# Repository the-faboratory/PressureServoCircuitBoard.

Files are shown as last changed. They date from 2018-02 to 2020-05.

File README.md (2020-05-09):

# Pneumatic Regulator git repository
This repository contains (hopefully) everything needed to replicate the pneumatic regulator presented in

J. W. Booth, J. C. Case, E. L. White, D. S. Shah, and R. Kramer-Bottiglio, “[An addressable pneumatic regulator for distributed control of soft robots](10.1109/ROBOSOFT.2018.8404892),” in 2018 IEEE International Conference on Soft Robotics (RoboSoft).

It will be called "pneumatic regulator" and "pressure regulator" interchangeably.

If you have comments, suggestions, or want additional information, including how to obtain a pre-programmed and pre-assembled pressure regulator, please contact Joran Booth at JoranBooth@gmail.com. Being a research lab affiliated with a non-profit university, we are unable to sell regulators through our Yale affiliations. However, we are exploring commercializing the boards out of a small garage operation, depending on interest levels and applicable laws.

## Getting Started

### Prerequisites

Download MPLAB IDE(http://www.microchip.com/mplab/mplab-x-ide), with the XC compilers.

A detailed programming guide, with notes on the PressureRegulator's state machine, is in repository_guide.docx.

There are two versions of the hardware, with different connectors: one with 0.1" headers, and one with a MOLEX connector.

### Installing / Using
Programming a device is as easy as 1,2,3,...4:
```
1. Open the PIC_I2C.X project in MPLAB.
2. Change the variable I2C_ADDRESS to contain 2x the address you want the Arduino to call your PIC. Example: Arduino talks to sensor at address 8. I2C_ADDRESS = 2x8 = 16
3. Click "clean and build" to make sure it is compiling properly for your computer. (If you get a compiler error, try opening project properties and use C standard 90 (Project properties -> XC8 Global Options -> C Standard))
4. Click "Make and Program Device Main Project", to download the program to your PIC using a PicIt3 (the 'red box').
```

## Testing The Firmware

For your first test, use the Arduino driver pneumatic_regulator_driver.ino, or the sample Arduino Wire library code. For your I2C pullup, use 3.3k or 4.7k.

## Explanation of files (see each file for details):

File/Directory |  Purpose |
----- | --------- |
arduino_driver | Folder containing sample Arduino driver for communicating with the pressure regulators
auxiliary_files | Additional documentation, and a Microchip I2C application note.
pcb_files | Eagle files, bill of materials, and gerber files (for PCB.ng) for both versions of the regulator: 0.1" headers, and MOLEX connector
Pic_I2C.X | Project folder for programming the pneumatic regulator's PIC microcontroller using MPLAB.
PicIt3_user_guide | [A guide to using the PICkit3](http://ww1.microchip.com/downloads/en/DeviceDoc/50002010B.pdf). Made by Microchip.
pressure_regulator_i2c.c | Firmware for the pressure regulator's PIC microcontroller, to control pressure manually or use Bang-Bang with a deadband to regulate the pressure at the output (i.e., in your actuator).
repository_guide.docx | An explanation of how to download firmware to a PIC, using this repository.

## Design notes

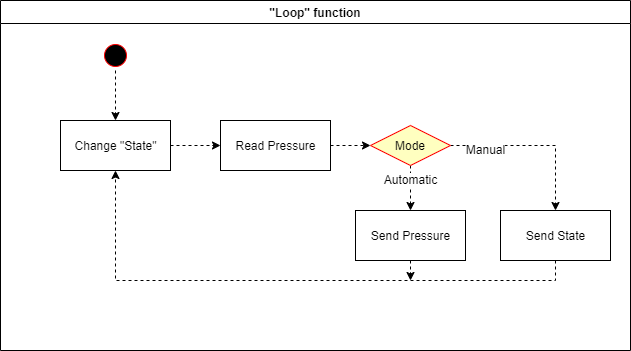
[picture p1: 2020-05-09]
auxiliary_files/pneumatic_regulator_state_flowchart.png

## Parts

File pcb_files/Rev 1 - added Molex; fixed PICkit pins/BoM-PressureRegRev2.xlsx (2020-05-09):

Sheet: 30PSI
Description | DigiKey Description | DigiKey part # | Manufacturer | Mfg part # | Qty | $/unit | Total | Packaging | Link
10K Ohm resistor | RES SMD 10K OHM 1% 1/10W 0603 | 311-10.0KHRCT-ND | Yageo | RC0603FR-0710KL | 2 | 0.015 | 0.03 | Cut reel | https://www.digikey.com/products/en?keywords=%20311-10.0KHRCT-ND%20
10uf Capacitor | CAP TANT 10UF 25V 20% 1206 | 478-8496-1-ND | AVX | F951E106MAAAQ2 | 1 | 0.766 | 0.766 | Cut reel | https://www.digikey.com/products/en?keywords=478-8496-1-ND
10uh Inductor | FIXED IND 10UH 230MA 1.3 OHM SMD | 490-6588-1-nd | Murata | LQH31CN100K03L | 2 | 0.685 | 1.37 | Cut reel | https://www.digikey.com/products/en?keywords=490-6588-1-nd
150 Ohm resistor | RES SMD 150 OHM 1% 1/10W 0603 | 311-150HRCT-ND | Yageo | RC0603FR-07150RL | 1 | 0.015 | 0.015 | Cut reel | https://www.digikey.com/products/en?keywords=490-6588-1-nd
1uf Capacitor | CAP CER 1UF 25V X5R 0603 | 311-1445-1-ND | Yageo | CC0603KRX5R8BB105 | 3 | 0.052 | 0.156 | Cut reel | https://www.digikey.com/products/en?keywords=311-1445-1-ND%20
Diode | DIODE GEN PURP 75V 200MA SOD523 | bas16xv2t5gosct-nd | ON Semiconductor | BAS16XV2T5G | 2 | 0.156 | 0.312 | Cut reel | https://www.digikey.com/products/en?keywords=bas16xv2t5gosct-nd
Cap 100uf | CAP ALUM 100UF 20% 35V SMD | pce5016ct-nd | Panasonic | EEE-FT1V101AP | 2 | 0.427 | 0.854 | Cut reel | https://www.digikey.com/products/en?keywords=pce5016ct-nd
Connection header | CONN HEADER 4POS 1.25MM R/A SMD | WM7622CT-ND | Molex | 532610471 | 1 | 1.038 | 1.038 | Cut reel | https://www.digikey.com/products/en?keywords=WM7622CT-ND
PIC microchip | IC MCU 8BIT 14KB FLASH 14-TSSOP | PIC16F1825T-I/STCT-ND | Microchip | PIC16F1825T-I/ST | 1 | 1.45 | 1.45 | Cut reel | https://www.digikey.com/products/en?keywords=PIC16F1825T-I%2FSTCT-ND
IC Voltage regulator 5V | IC REG LINEAR 5V 100MA SOT223 | 576-1249-1-nd | Microchip | MIC5200-5.0YS-TR | 1 | 1.08 | 1.08 | Cut reel | https://www.digikey.com/products/en?keywords=576-1249-1-nd
Green LED | LED GREEN CLEAR 0603 SMD | 160-1435-1-nd | Lite-On | LTST-C190KGKT | 1 | 0.196 | 0.196 | Cut reel | https://www.digikey.com/products/en?keywords=160-1435-1-nd
n-ch Mosfet 100v 17a | MOSFET N-CH 100V 17A DPAK | irlr3410pbfct-nd | International Rectifier | IRLR3410TRPBF | 2 | 0.88 | 1.76 | Cut reel | https://www.digikey.com/products/en?keywords=irlr3410pbfct-nd
Parker X-valve | N/A - select 30psi, 3 way universal, long pins, 12 VDC | N/A | Parker | 912-000001-003 | 2 | 37 | 74 | Tray | http://ph.parker.com/us/12051/en/x-valve-miniature-pneumatic-solenoid-valve
Pressure sensor, 5V, 30psi | SENSOR PRESS 30PSIG ANALOG | 480-4490-ND | Honeywell | ASDXRRX030PGAA5 | 1 | 46.95 | 46.95 | Tray | https://www.digikey.com/product-detail/en/honeywell-sensing-and-productivity-solutions/ASDXRRX030PGAA5/480-4490-ND/2566947
 |  |  |  |  |  |  | 129.977

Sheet: 100PSI
These parts have not been tested together! Power requirements and orifice sizes should be identical.
Description | DigiKey Description | DigiKey part # | Manufacturer | Mfg part # | Qty | $/unit | Total | Packaging | Link
10K Ohm resistor | RES SMD 10K OHM 1% 1/10W 0603 | 311-10.0KHRCT-ND | Yageo | RC0603FR-0710KL | 2 | 0.015 | 0.03 | Cut reel | https://www.digikey.com/products/en?keywords=%20311-10.0KHRCT-ND%20
10uf Capacitor | CAP TANT 10UF 25V 20% 1206 | 478-8496-1-ND | AVX | F951E106MAAAQ2 | 1 | 0.766 | 0.766 | Cut reel | https://www.digikey.com/products/en?keywords=478-8496-1-ND
10uh Inductor | FIXED IND 10UH 230MA 1.3 OHM SMD | 490-6588-1-nd | Murata | LQH31CN100K03L | 2 | 0.685 | 1.37 | Cut reel | https://www.digikey.com/products/en?keywords=490-6588-1-nd
150 Ohm resistor | RES SMD 150 OHM 1% 1/10W 0603 | 311-150HRCT-ND | Yageo | RC0603FR-07150RL | 1 | 0.015 | 0.015 | Cut reel | https://www.digikey.com/products/en?keywords=490-6588-1-nd
1uf Capacitor | CAP CER 1UF 25V X5R 0603 | 311-1445-1-ND | Yageo | CC0603KRX5R8BB105 | 3 | 0.052 | 0.156 | Cut reel | https://www.digikey.com/products/en?keywords=311-1445-1-ND%20
Diode | DIODE GEN PURP 75V 200MA SOD523 | bas16xv2t5gosct-nd | ON Semiconductor | BAS16XV2T5G | 2 | 0.156 | 0.312 | Cut reel | https://www.digikey.com/products/en?keywords=bas16xv2t5gosct-nd
Cap 100uf | CAP ALUM 100UF 20% 35V SMD | pce5016ct-nd | Panasonic | EEE-FT1V101AP | 2 | 0.427 | 0.854 | Cut reel | https://www.digikey.com/products/en?keywords=pce5016ct-nd
Connection header | CONN HEADER 4POS 1.25MM R/A SMD | WM7622CT-ND | Molex | 532610471 | 1 | 1.038 | 1.038 | Cut reel | https://www.digikey.com/products/en?keywords=WM7622CT-ND
PIC microchip | IC MCU 8BIT 14KB FLASH 14-TSSOP | PIC16F1825T-I/STCT-ND | Microchip | PIC16F1825T-I/ST | 1 | 1.45 | 1.45 | Cut reel | https://www.digikey.com/products/en?keywords=PIC16F1825T-I%2FSTCT-ND
IC Voltage regulator 5V | IC REG LINEAR 5V 100MA SOT223 | 576-1249-1-nd | Microchip | MIC5200-5.0YS-TR | 1 | 1.08 | 1.08 | Cut reel | https://www.digikey.com/products/en?keywords=576-1249-1-nd
Green LED | LED GREEN CLEAR 0603 SMD | 160-1435-1-nd | Lite-On | LTST-C190KGKT | 1 | 0.196 | 0.196 | Cut reel | https://www.digikey.com/products/en?keywords=160-1435-1-nd
n-ch Mosfet 100v 17a | MOSFET N-CH 100V 17A DPAK | irlr3410pbfct-nd | International Rectifier | IRLR3410TRPBF | 2 | 0.88 | 1.76 | Cut reel | https://www.digikey.com/products/en?keywords=irlr3410pbfct-nd
Parker X-valve | N/A - select 100psi, 3 way universal, long pins, 12 VDC | N/A | Parker | 912-000001-021 | 2 | 37 | 74 | Tray | http://ph.parker.com/us/12051/en/x-valve-miniature-pneumatic-solenoid-valve
Pressure sensor, 5V, 100psi | SENSOR PRESS 100PSIG ANALOG | 480-3748-ND | Honeywell | ASDXRRX100PGAA5 | 1 | 49.27 | 49.27 | Tray | https://www.digikey.com/product-detail/en/honeywell-sensing-and-productivity-solutions/ASDXRRX100PGAA5/480-3748-ND/2566950
 |  |  |  |  |  |  | 132.297

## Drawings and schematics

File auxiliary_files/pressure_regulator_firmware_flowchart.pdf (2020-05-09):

11/15/2017 | pressureRegulatorI2cFlowchart.xml

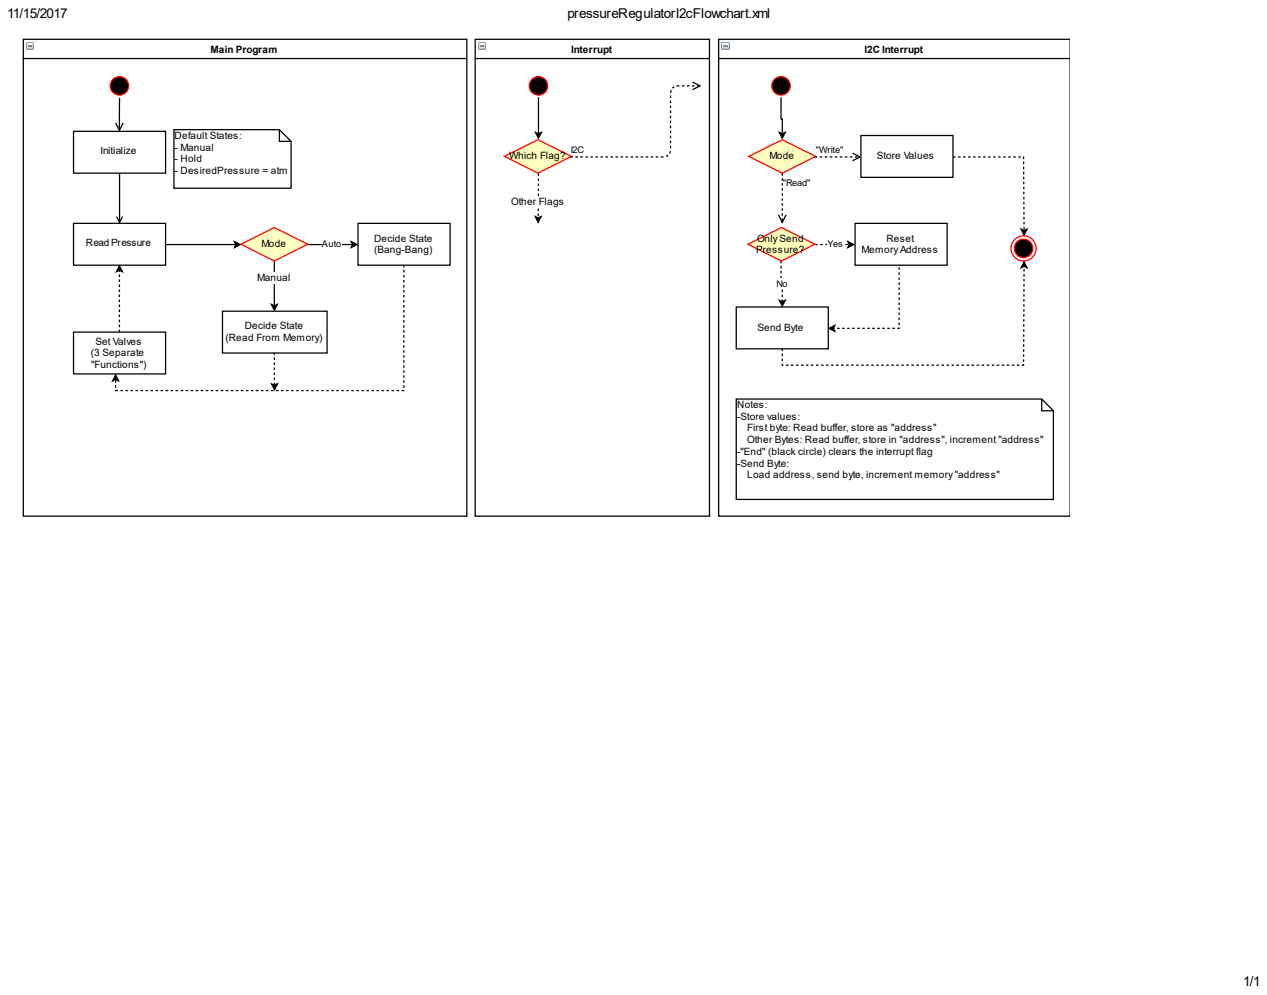
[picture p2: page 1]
Main Program; Initialize; Read Pressure; Default States: - Manual - Hold - DesiredPressure = atm; Auto; Manual; Mode; Decide State (Bang-Bang); Set Valves (3 Separate "Functions"); Interrupt; Which Flag?; I2C Interrupt; "Write"; "Read"; Store Values; Yes; Only Send Pressure?; Send Byte; Other Flags

Reset Memory Address

Decide State
(Read From Memory)

Notes:
-Store values:
First byte: Read buffer, store as "address" Other Bytes: Read buffer, store in "address", increment "address"

-"End" (black circle) clears the interrupt flag
-Send Byte:
Load address, send byte, increment memory "address"

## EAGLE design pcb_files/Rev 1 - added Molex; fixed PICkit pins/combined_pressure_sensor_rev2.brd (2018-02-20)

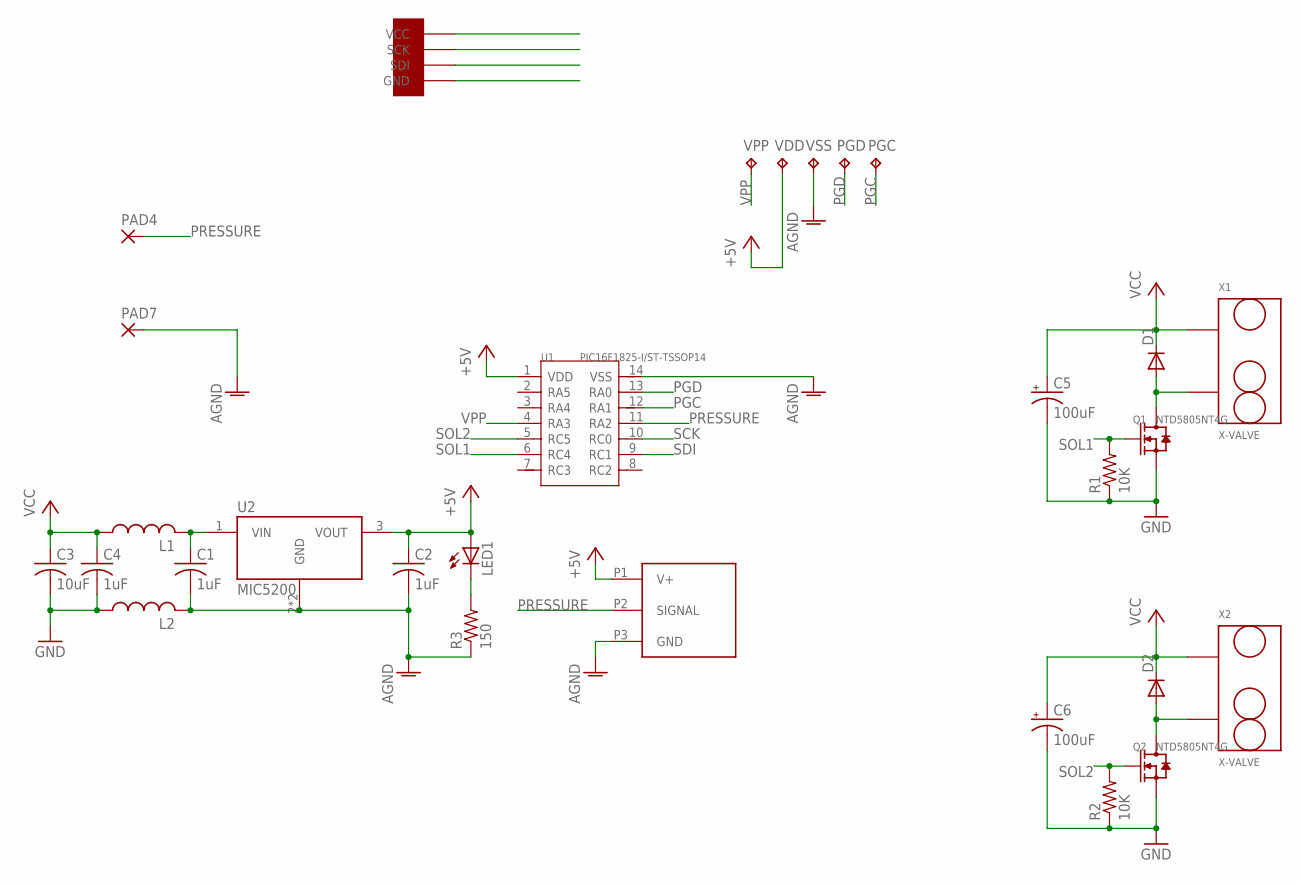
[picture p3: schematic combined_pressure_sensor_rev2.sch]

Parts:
C1, C2, C4: 1uF; C0603
C3: 10uF; C1206
C5, C6: 100uF; 153CLV-0605
D1, D2: DIODE-SOD523; SOD523
L1, L2: L-USL1206; L1206
LED1: LEDCHIP-LED0603; CHIP-LED0603
PAD4, PAD7: SMD2; SMD1,27-2,54
PGC: TPB1,27; B1,27
PGD: TPB1,27; B1,27
Q1, Q2: NTD5805NT4G; DPAK
R1, R2: 10K; R0603
R3: 150; R0603
U1: PIC16F1825-I/ST-TSSOP14; TSSOP14-0.65-5X4.4MM
U2: MIC5200; SOT223
U$1: PICOBLADE4POS1.25MMRIGHTANGLESURFACE; PICOBLADE4POSMALEHEADER
U$3: ASDX
VDD: TPB1,27; B1,27
VPP: TPB1,27; B1,27
VSS: TPB1,27; B1,27
X1, X2: X-VALVE

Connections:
+5V: C2.1, LED1.A, U1.1 (VDD), U2.3 (VOUT), U$3.P1 (V+), VDD.TP
AGND: C1.2, C2.2, L2.2, PAD7.1, R3.1, U1.14 (VSS), U2.2 (GND), U2.4 (GND), U$3.P3 (GND), VSS.TP
GND: C3.2, C4.2, C5.-, C6.-, L2.1, Q1.2 (S), Q2.2 (S), R1.1, R2.1, U$1.GND
unnamed: D1.A, Q1.3 (D), X1.P$2
unnamed: D2.A, Q2.3 (D), X2.P$2
unnamed: C1.1, L1.2, U2.1 (VIN)
unnamed: LED1.C, R3.2
PGC: PGC.TP, U1.12 (RA1)
PGD: PGD.TP, U1.13 (RA0)
PRESSURE: PAD4.1, U1.11 (RA2), U$3.P2 (SIGNAL)
SCK: U1.10 (RC0), U$1.SCK
SDI: U1.9 (RC1), U$1.SDI
SOL1: Q1.1 (G), R1.2, U1.6 (RC4)
SOL2: Q2.1 (G), R2.2, U1.5 (RC5)
VCC: C3.1, C4.1, C5.+, C6.+, D1.C, D2.C, L1.1, U$1.VCC, X1.P$1, X2.P$1
VPP: U1.4 (RA3), VPP.TP

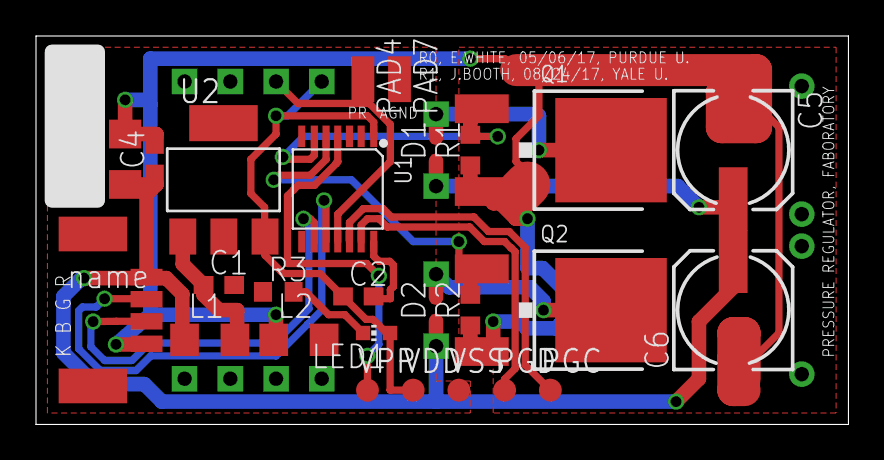
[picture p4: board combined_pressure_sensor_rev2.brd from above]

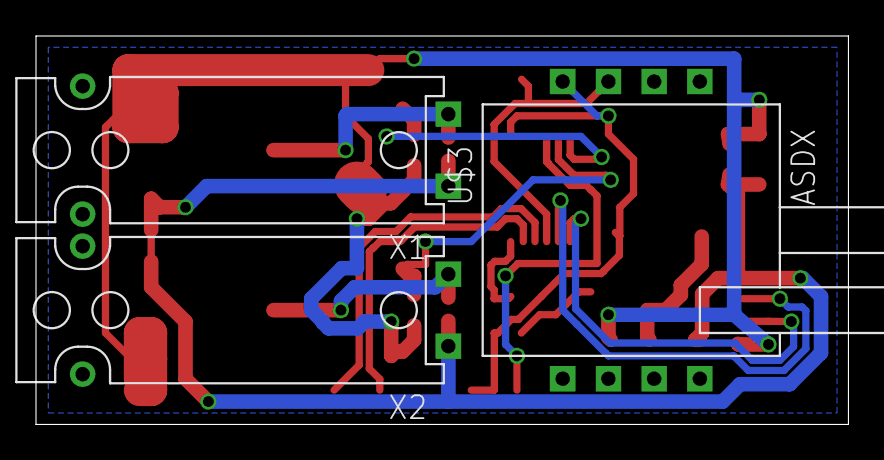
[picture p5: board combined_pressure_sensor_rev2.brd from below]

Board: 2 copper layers, 45.1 x 21.6 mm, 29 parts (3 on the bottom side), 16 nets.

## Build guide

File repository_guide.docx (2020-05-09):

Last edited 2020-05-09 by Dylan Shah.

# 1. Programming a PIC (and how to use I2C)

General Notes:

- Steps 1-8 describe MPLab and circuit setup. Step 9 describes communication methods.
- This tutorial is written for the capacitor board, but is mostly applicable to all Faboratory circuit boards with a PIC microcontroller
1. Power circuit board with an external power supply of 5.00 volts, at least 10 mA. The Arduino 5V output line is insufficient. (Limit the circuit to 100 mA or less, to avoid frying the board in case of short-circuit. If four sensors are plugged in and one is being programmed by the PICkit3, <0.013 A will be used.) Plug PICkit 3 into PC.

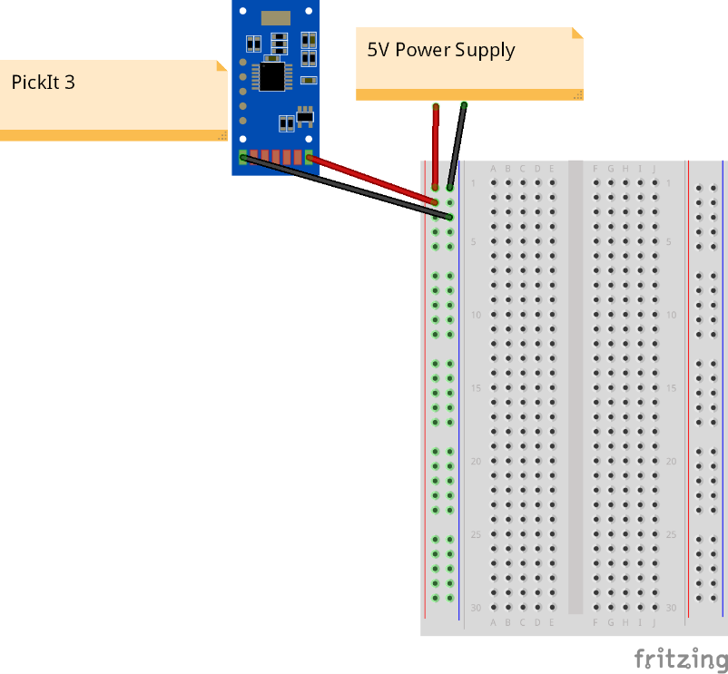
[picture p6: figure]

Figure 1. A suggested circuit. The blue PCB is the capacitor board or a pressure regulator. The white board is a breadboard.

2. Open Pic project <pic_i2c_project > in MPLab X IDE
3. Double-click the relevant “C” (.c) file to open it. In line 77, edit i2c_address to your desired address. In the photo below, the Arduino will communicate with address 99. It is stored in the PIC as address 198, since the Arduino automatically “shifts left” the address bits, i.e. it multiplies by 1 binary bit = value of 2.

Figure 2. Edit the I2C_ADDRESS variable.

4. Make sure there aren’t any hard-coded filepaths in the files, by right-clicking the project and doing “Clean and Build”

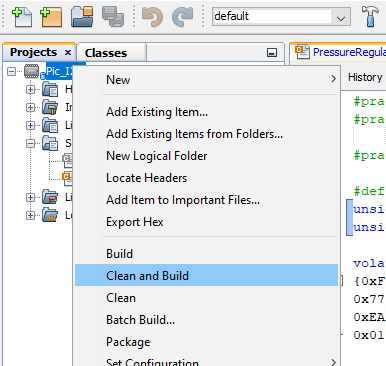
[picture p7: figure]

Figure 3. Prepare the project with “Clean and Build”

5. Set the PCB on a stable surface and firmly place the metal leads of the red PICkit 3 on the 5 circular pads of your PCB (Figure 4). Make sure all 5 leads contact their appropriate pad (but don’t break them).

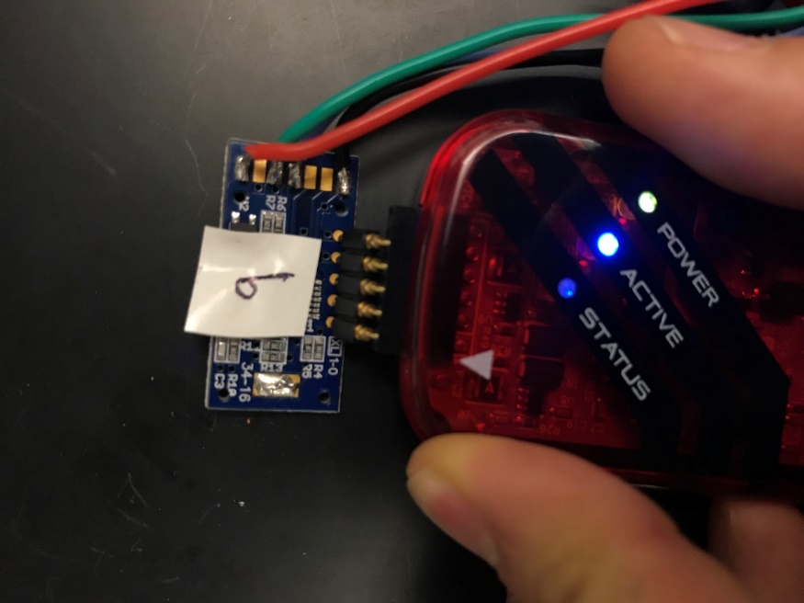
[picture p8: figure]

Figure 4. Connecting the PICit3 to the PCB.

6. Keeping the pads pressed, download to device using "Make and Debug Program Device".

Figure 5. Make and Debug Program Device

  a. If you didn’t already plug in the PICit3, a window will pop up. Plug in your PICit3, select it in the menu, and click “OK”.

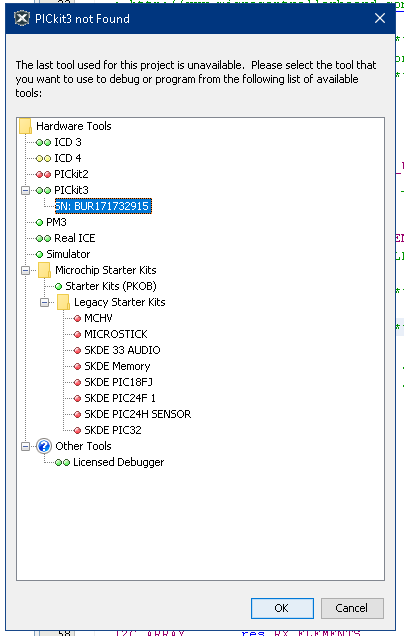
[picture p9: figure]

Figure 6. Selecting your PICkit3

  b. The console (probably at the bottom of your screen) will give you a message like “BUILD FAILED” or “BUILD SUCCESSFUL”. If the build failed , right-click your Project, select “clean and build”, and repeat this step.
    i. Other troubleshooting steps: 1. make sure you excluded all unnecessary files. 2. Make sure your board is powered by an external power supply, not the Arduino. 3. “Advanced” users: debug the firmware code.

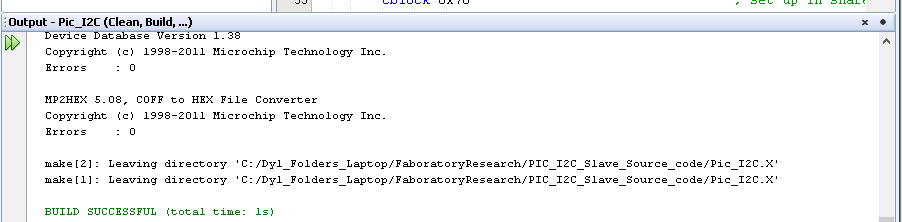
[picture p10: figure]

Figure 7. A “build successful” message.

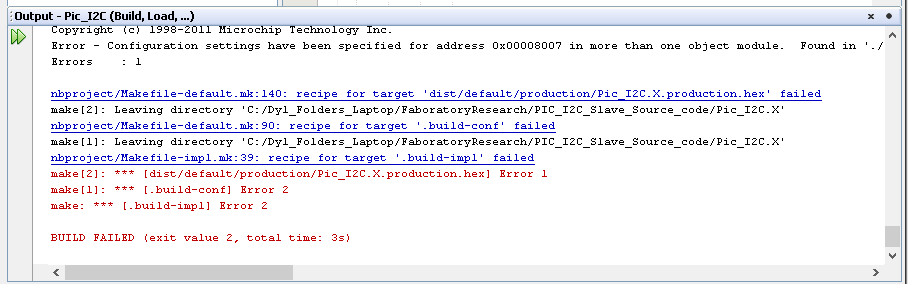
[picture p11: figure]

Figure 8. A "build failed” message.

7. Once it shows “build successful”, the console will clear and begin showing things like “Connecting to MPLAB PICkit 3”.

Figure 9. Connecting to PICkit 3

8. Some errors might show up.
  a. Basically , return to Step 4. Read the rest of bullet-point 8’s sub-bullets for additional tips.
  b. Shows red “Target device was not found…” Return to Step 4 (i.e, connect PIC and PICkit3, Make and Download…). Make sure to have good contact between each PICkit3 metal lead and the PCB’s corresponding circular contact.

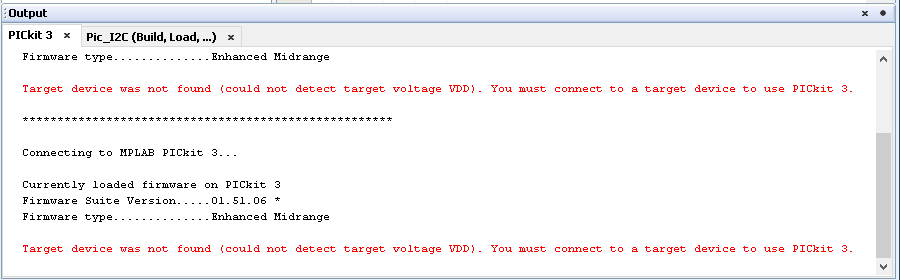
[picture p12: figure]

Figure 10. Target device not found.

  c. Popup similar to “Target Device ID (0x0) is an Invalid Device ID…”. DO NOT continue programming. Click Cancel, and return to step 4. Continuing can sometimes make the PIC un-programmable, but “when and why” is not well docmumented.

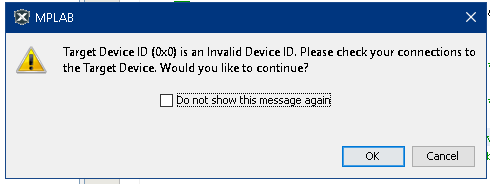
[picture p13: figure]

Figure 11. Target Device ID Invalid

9. Programming is complete when console displays “verify/program complete”.

Figure 12. Program/Verify complete

10. Optional: lift leads off of pads; power-cycle circuit. (I.e. turn the power supply off then on.) Sometimes the PIC will be put in a harmless but nonresponsive state during programming.
11. Connect the appropriate pins to an I2C circuit (“bus”). Arduino: A4 (SDA)=blue, A5(SCL) = green. Optionally, adjust so the PIC is powered by the Arduino. An example circuit is shown below. Typically I use 3.3KOhm pull-up resistors (https://electronics.stackexchange.com/questions/1849/is-there-a-correct-resistance-value-for-i2c-pull-up-resistors).

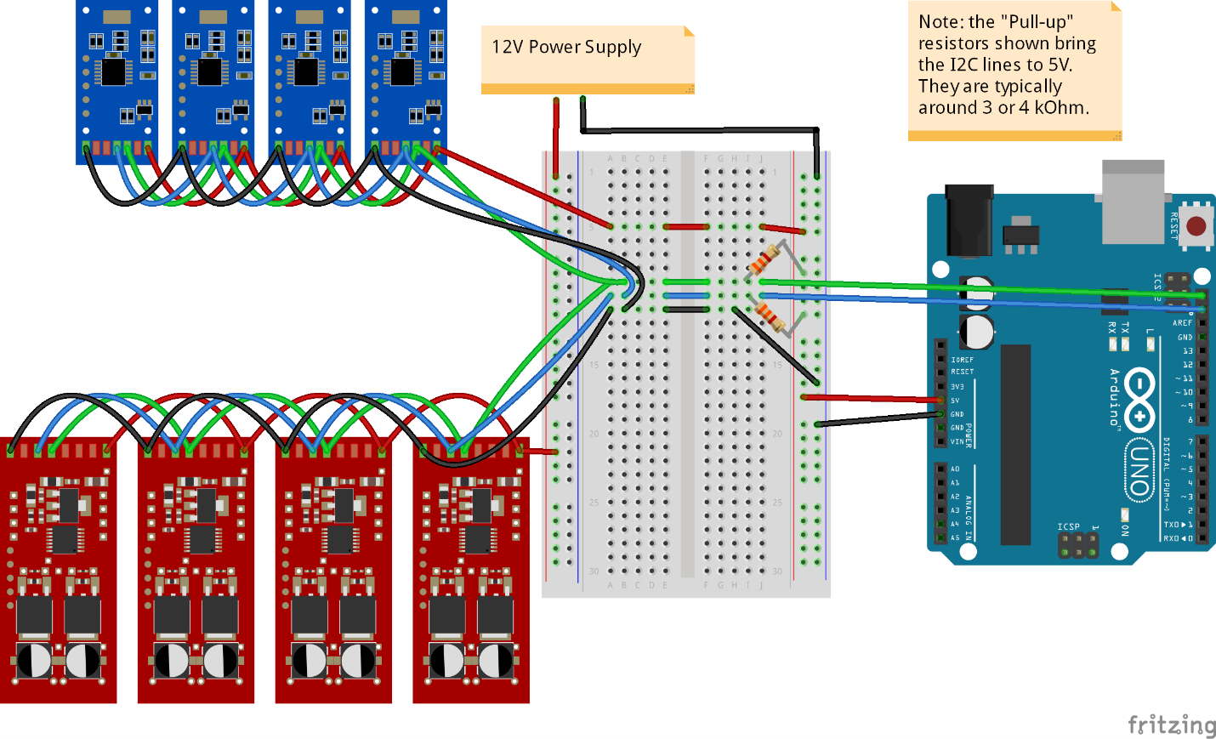
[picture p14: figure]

Figure 13. An example circuit.

12. Ready to communicate! Check the PIC firmware or repository README for an explanation of available interfaces/commands. Options:
  a. Arduino → PIC. Use the Arduino driver for your PIC firmware (in the Faboratory GitHub repository “Sensory-Active-Skin-Controller”) , or the sample Arduino Wire library code.
  b. PC → Arduino → PIC. Use your favorite Python, MATLAB, or terminal to interface with an arduino over Serial, which will communicate with the PIC. Talk to labmates.

# 2. Available Controllers for the pressure regulators

The pressure regulators can be controlled manually or “automatically” (Figure 15). Manually allows you to set the regulator to “Inflate”, “hold”, or “release”, while automatic mode implements a three-state bang-bang controller (Figure 14). We only switch from one state (green ellipsoid) to another if the condition along the transition arrow is met. Basically, the system tries to bound the error to be lower in magnitude than half of a “band width”. Abbreviations:

S = sensor data. SP = set point. BW = band width. UB = upper bound = SP + BW/2. LB = lower bound = SP – BW/2

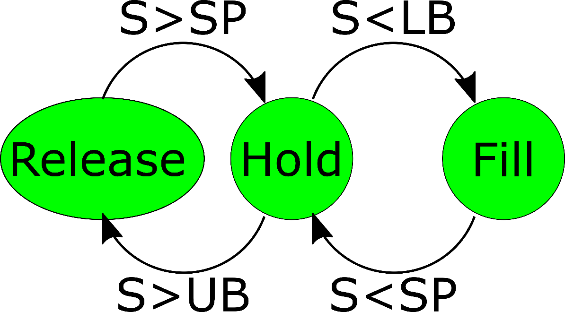
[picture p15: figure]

Figure 14. Automatic mode state diagram


Figure 15. Control modes flowchart

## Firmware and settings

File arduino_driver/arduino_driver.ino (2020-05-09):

/*************************************
  cap_sensor_driver.ino

  This driver is for testing pneumatic regulator(s). Assumes your PIC firmware will send, in sequence, the memory located at [the most recent sent index] upon a read request. (All commonly-used firmware as of 2019-10-29)
  Writes state to and reads pressure from a pressure regulator.
  Typical parameters a user wants to edit are marked by **USER**

  TODO:
     1. (Low priority) Verify that the Arduino won't send more than 2 bytes to the pressure regulator. That could lead to a data race (overwrite pressure reading on PIC)

  Written by Dylan Shah. Last edited 2019-10-29 YMD.
*************************************/


// ***** 1. Import libraries *****
#include <Wire.h>


// ***** 2. Initialize Variables *****
// 2.1. System configuration variables
const int NUM_ACTUATORS = 2; // **USER**
int regulator_addresses[NUM_ACTUATORS] = {4, 29}; // **USER**

// 2.2. Indices for the PIC's internal memory (PIC has a chunk of program memory reserved for storing variables that external devices are allowed to modify.)
const int INDEX_SETPOINT_HIGH_BYTE = 16; // Set point (stored unit = "bits of ADC readings"). Default set point is atmospheric pressure (-0.147 [PSI])
const int INDEX_DESIRED_STATE = 18; // Our desired state. This is only active during manual mode. State. 0 = Release, 1 = Hold (default, both valves off), 2 = Inflate.
const int INDEX_PRESSURE_SENSOR_HIGH_BYTE = 19; // High byte of the pressure sensor
const int INDEX_HALF_BAND = 21; // 1/2*How wide our bang-bang deadband should be. Default Half-band is 10 [ADC values] = 2.94 [PSI]
const int INDEX_OPERATION_MODE = 22; // What mode should we operate in? 0 = Automatic. 1 = manual (default)
const int INDEX_ONLY_SEND_PRESSURE = 23; // If == 0, then the i2cArray can be read. ElseIf == 1, every read results in reading pressure (default).

// 2.3. General variables
const int nBytes = 2; // How many bytes to read
float values[NUM_ACTUATORS]; // Array of received data
float filtered_values[NUM_ACTUATORS]; // Array of filtered sensor data
int iteration_state = 0; // State in the iteration (used for cycling between commands)
bool change_state = false; // Should we change state?
unsigned long current_millis = 0.0; // The current program time
unsigned long command_delay = 1000; // How long to delay between commands [ms]
unsigned long cycle_delay = 10; // How long to delay between cycles [ms]

// 2) Pressure Regulator Variables
const int AUTOMATIC = 0;
const int MANUAL = 1;
int control_mode = AUTOMATIC; // **USER**
bool only_send_pressure = 0; // **USER**
float command = 0; // FLOAT. Was unsigned long
unsigned long command_to_send = 0; // Use unsigned int to allow bitshift operator
const int halfBand = 3; // **USER** 1/2 * how wide our bang-bang deadband should be
float expConst = .9; // **USER** Decay constant for the optional exponential filter


// ***** 3. Set up Arduino *****
void setup() {
  Wire.begin();        // join i2c bus (address optional for master)
  Serial.begin(2000000);  // start serial for output
  // Wire.setClock(400000); // Change I2C speed to 4kHz
  
  current_millis = millis(); // Initial time
  for (int actuator = 0; actuator < NUM_ACTUATORS; actuator++) {
    write_i2c(regulator_addresses[actuator], INDEX_OPERATION_MODE, control_mode); // Send pic firmware mode to the actuator
    write_i2c(regulator_addresses[actuator], INDEX_HALF_BAND, halfBand); // Send inHalfBand to the actuator
    write_i2c(regulator_addresses[actuator], INDEX_ONLY_SEND_PRESSURE, only_send_pressure); // Send "don't only send pressure" to the actuator
  }
}



// ***** 4. Change pressure, read sensors and send readings to PC over Serial, forever *****
void loop() {

  // Periodically, change command
  if (millis() > current_millis + command_delay) {
    current_millis = millis();
    iteration_state++;
    change_state = true;
  }

  // Write to and read from regulators
  for (int actuator = 0; actuator < NUM_ACTUATORS; actuator++) {
    read_pressure_regulator(regulator_addresses[actuator], filtered_values[actuator], expConst, values[actuator]); // Read regulator's pressure

    // Change command if it is a "command cycle"
    if (change_state) {
      // Send a set point to the actuator, if it is in automatic mode
      if (control_mode == AUTOMATIC) {
        command = 4 * (iteration_state % 3)+4; // Command to send [psi]
        float command_to_volt = psi_to_volt(command); // Convert to volts
        command_to_send = volt_to_ten_bit(command_to_volt) >> 2; // Convert to bits, and only send high byte (high 8 bits)
        write_i2c(regulator_addresses[actuator], INDEX_SETPOINT_HIGH_BYTE, command_to_send); // Send command to the actuator

        // Print to serial, for debugging
        Serial.print(command_to_volt);
        Serial.print("\t");
        Serial.print(command_to_send);
        Serial.print("\n");
      }

      // Send a desired state, if in manual mode
      if (control_mode == MANUAL) {
        command = 2 - iteration_state % 3; // Only valid states are 0,1,2. PIC will also 'modulo' on its own.
        write_i2c(regulator_addresses[actuator], INDEX_DESIRED_STATE, command); // Send command to the actuator
      }
    }
  }

  finishCycle(); // Print to serial, and delay for 'cycle_delay' [ms]
}



// ***** 5. Helper Functions *****
void finishCycle() {
  // Print over Serial, clear 'change state' flag and delay for 'cycle_millis' [ms]
  Serial.print(command);
  Serial.print("\t");
  Serial.println("");
  for (int actuator = 0; actuator < NUM_ACTUATORS; actuator++) {
    Serial.print(regulator_addresses[actuator]); Serial.print("\t");
    Serial.print(values[actuator]); Serial.print("\t");
  }
  change_state = false;
  delay(cycle_delay);
}


// 5.1. Communicate with Pressure Regulator
void read_pressure_regulator(const int &in_address, float &in_filtered, const float &in_exp_constant, float &in_reading) {
  // Read the pressure regulator's air-pressure sensor, and filter it.

  // If we are not in "only_send_pressure" mode, then tell the PIC which address to read from.
  if (!only_send_pressure) {
    Wire.beginTransmission(in_address); // Prepare internal variables
    Wire.write(INDEX_PRESSURE_SENSOR_HIGH_BYTE); // Write memory location to buffer
    Wire.endTransmission(); // Transmit
  }

  // Request and process the pressure sensor's reading
  Wire.requestFrom(in_address, 2); byte b1_local = Wire.read(); byte b2_local = Wire.read(); // Read data
  float temp_reading = ((float)b1_local * 256 + (float)b2_local) / pow(2, 6); // Only keep 10 high bits. Convert to voltage
  temp_reading = ten_bit_to_volt(temp_reading);
  in_reading = volt_to_psi(temp_reading);
  in_filtered = (in_exp_constant * in_filtered + (1 - in_exp_constant) * in_reading); // Apply an exponential filter
}


void write_i2c(int in_address, int in_index, int in_value) {
  // Write data to the device over I2C
  Wire.beginTransmission(in_address); // Prepare internal variables
  Wire.write(in_index); // Write memory location to buffer
  Wire.write(in_value); // Write value to buffer
  Wire.endTransmission(); // Transmit
}
// End communicate with Pressure Regulator


// 5.2. Unit conversions
float ten_bit_to_volt(float in_ten_bit) {
  // Convert a 10-bit "5V source 10 bit ADC reading" to voltage.
  float volts = in_ten_bit * 5 / pow(2, 10);
  return volts;
}


unsigned long volt_to_ten_bit(float in_volts) {
  // Convert from 5V to 10 bit ADC reading (scaled as 2^10 distinct values over 5 volts)
  unsigned long tenBit = in_volts * pow(2, 10) / 5;
  return tenBit;
}


float volt_to_psi(float in_volts) {
  // Convert voltage reading to pressure [psi]
  // This calibration function is specific to our pressure regulator. "ASDX RR X 030PG A A 5". Read from ASDX series spec sheet, p.4.
  float max_pressure = 30;
  float min_pressure = 0;
  float supply_voltage = 5;
  float transfer_function_limits = 0.1;
  float psi = ((in_volts - transfer_function_limits * supply_voltage) * (max_pressure - min_pressure)) / (0.8 * supply_voltage) + min_pressure;
  return psi;
}


float psi_to_volt(float in_psi) {
  // Convert pressure to voltage reading [V]
  // This calibration function is specific to our pressure regulator. "ASDX RR X 030PG A A 5". Read from ASDX series spec sheet, p.4.
  float max_pressure = 30;
  float min_pressure = -30;
  float supply_voltage = 5; // supply voltage
  float transfer_function_limits = 0.1;
  float volt = 0.8 * supply_voltage / (max_pressure - min_pressure) * (in_psi - min_pressure) + transfer_function_limits * supply_voltage;
  return volt;
}
// End Unit conversions

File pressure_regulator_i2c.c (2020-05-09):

/*******************************************************************************  
This C file runs on the PCB "Pressure Regulator Rev. 0" for networked 
control of a pneumatic valve. Operation modes: automatic (0), manual (1).
A master can read the pressure data, which is a 10 bit adc reading of the pressure sensor.
Pic stores this as 16 bits. This means you should drop the low 6 bits of the data.
Pressure sensor calibration equation:
volts = 0.8*V_s/(P_max-P_min)*(P_applied - P_min) + 0.1*V_s
Power consumption: ~0.021A in "hold state" (valves off); each valve uses ~0.074 A

Typical parameters a user wants to edit are marked by **USER**

Communication:
    - To write memory, write [the memory address] followed by [the data].
    - To read memory, write [the memory address] and then read [the desired number of data bytes].


Automatic mode (3-state bang-bang), typical use case: 
    1. Arduino send INDEX_OPERATION_MODE (22), followed by an operation mode (0 for 
    automatic)//
    2. Arduino send INDEX_SETPOINT_HIGH_BYTE (16), followed by a desired pressure (0 through 255. 126 is atmospheric pressure). 
    3. Arduino send value of INDEX_PRESSURE_SENSOR_HIGH_BYTE (19). 41
    4. Arduino request 2 bytes. PIC sends two bytes of pressure data.

Manual mode (arduino directly controls state), typical use case: 
    1. Arduino send INDEX_OPERATION_MODE (22), followed by an operation mode (1 for 
    manual)//
    2. Arduino send INDEX_DESIRED_STATE (16), followed by a desired state (State options: 0 = release, 1 = hold, 2 = inflate)
    3. Arduino send value of INDEX_PRESSURE_SENSOR_HIGH_BYTE (19). 
    4. Arduino request 2 bytes. PIC sends two bytes of pressure data.

Circuit information
    Inputs
        RA2 - Pressure Feedback. Circuit diagram "PRESSURE"

    Outputs
        RC4 - release. Circuit diagram "SOL 1"
        RC5 - inflate. Circuit diagram "SOL 2"

    ICSP Programming
        RA0 - ICSPDAT = PGD
        RA1 - ICSPCLK = PGC
        RA3 - VPP

    I2C
        RC0 I2C_CLK = SCK
        RC1 I2C_DAT = SDI

/******************************************************************************/
#include <pic.h> 
#include <xc.h>

#include <pic16f1825.h> // Dyl define registers and aliases

// CONFIG1
#pragma config FOSC = INTOSC    // INTOSC oscillator: I/O function on CLKIN pin
#pragma config WDTE = ON        // Watchdog Timer Enable (WDT enabled) Dyl off
#pragma config PWRTE = ON       // Power-up Timer Enable (PWRT enabled) Dyl Off
#pragma config MCLRE = ON       // MCLR/VPP pin function is MCLR
#pragma config CP = ON          // Program memory code protection is enabled Dyl Off
#pragma config CPD = ON         // Data memory code protection is enabled Dyl off
#pragma config BOREN = ON       // Brown-out Reset enabled
#pragma config CLKOUTEN = OFF   // CLKOUT function is disabled. Dyl On
                                // I/O or oscillator function on the CLKOUT pin
#pragma config IESO = ON        // Internal/External Switch-over mode is enabled
#pragma config FCMEN = ON       // Fail-Safe Clock Monitor is enabled

// CONFIG2
#pragma config WRT = OFF        // Flash Memory Self-Write Protection off
//#pragma config VCAPEN = OFF     // All VCAP pin functionality is disabled
#pragma config PLLEN = ON       // PLL Enable (4x PLL enabled)
#pragma config STVREN = ON      // Stack Overflow/Underflow will cause a Reset
#pragma config BORV = LO        // Brown-out Reset Voltage (Vbor)
                                // low trip point selected.
#pragma config LVP = ON         // Low-Voltage Programming enabled

#define RX_ELMNTS   32
unsigned char i2c_address =     4*2; // slave address (doubled) ** USER Should Modify **
unsigned int DELAY_MS = 30; // delay [ms]. This can be used to reduce chatter on the regulators * USER can modify *

volatile unsigned char I2C_Array[RX_ELMNTS] =   // array for master to write to
{0xFF, 0xEE, 0xDD, 0xCC, 0xBB, 0xAA, 0x99, 0x88,
0x77, 0x66, 0x55, 0x44, 0x33, 0x22, 0x11, 0xFA,
0xEA, 0xDA, 0xCA, 0xBA, 0xFB, 0xFC, 0xFD, 0xFE,
0x01, 0x02, 0x03, 0x04, 0x05, 0x06, 0x07, 0x08};

unsigned int index_i2c = 0;            // used as an index pointer in array
unsigned char junk = 0;                // used to place unnecessary data
unsigned char first = 1;               // used to determine whether data address 
                                       // location or actual data


// Global algorithm variables
#define INDEX_SETPOINT_HIGH_BYTE    16 // High byte of our desired actuator set point.  Default setpoint is atmospheric pressure (2.5V -> HighByte = 127 = -0.147 PSI)
#define INDEX_SETPOINT_LOW_BYTE 17 // Low byte of our desired actuator power
#define INDEX_DESIRED_STATE    18 // State. 0 = Release, 1 = Hold, 2 = Inflate. Our desired state. This is only active during manual mode.  Default valve state is hold (both valves off).
#define INDEX_PRESSURE_SENSOR_HIGH_BYTE 19 // High byte of our actuator's pressure sensor
#define INDEX_PRESSURE_SENSOR_LOW_BYTE 20  // Low byte of our actuator's pressure sensor
#define INDEX_HALF_BAND 21 // 1/2*How wide our bang-bang deadband should be. Default Half-band is 10 [ADC values] = 2.94 [PSI]
#define INDEX_OPERATION_MODE 22 // What mode should we operate in? automatic = 0. manual = 1.  Default mode is manual
#define INDEX_ONLY_SEND_PRESSURE 23 // If == 0, then the i2cArray can be read. ElseIf == 1, every read results in reading pressure. Default read mode is "only send pressure"
#define Nop() {_asm nop _endasm} // Dyl define the NOP function for doing nothing https://www.microchip.com/forums/m156162.aspx
#define _XTAL_FREQ 32000000 // internal oscillator: 32 MHz
unsigned int setPointHigh;       // high byte of the setpoint
unsigned int setPointLow; // low byte of the setpoint
unsigned int pressureHigh;    // high byte of the ADC reading
unsigned int pressureLow; // low byte of the ADC reading
unsigned int state;      // State options: 0 = release, 1 = hold, 2 = inflate
unsigned int countdown;      // acquisition timer for the ADCs
unsigned int tempIndex;   // Temporary index
unsigned int halfBand;    // 1/2*How wide our bang-bang deadband should be
unsigned int topBand;     // Top of our deadBand
unsigned int bottomBand;  // Bottom of our deadBand
unsigned int operationMode;   // What mode should we operate in? bangBang = 0. stateMachine = 1
unsigned int onlySendPressureBool; // If == 0, then the i2cArray can be read. ElseIf == 1, every read results in reading pressure


// Function declarations (self-explanatory)
void initialize(void);
void manualMode(void);
void automaticMode(void);
void currentlyReleasing(void);
void currentlyHolding(void);
void currentlyInflating(void);
void release(void);
void hold(void);
void inflate();
void sampleDelay(void);
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

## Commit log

2018-02-20 Add files via upload
    These are the base files for the pressure regulator.
    [combined_pressure_sensor_rev1.brd, combined_pressure_sensor_rev1.sch]
2018-02-20 Add files via upload
    Adds the arduino files for connecting to the servo.
2020-05-09 Clean up, add c firmware, add .gitignore, add bill of materials and gerber files
    [BoM - pressure_regulator_rev2.xlsx, combined_pressure_sensor_rev1.brd, combined_pressure_sensor_rev1.sch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]
2020-05-09 minor readme updates
    [BoM-PressureRegRev2.xlsx, combined_pressure_sensor_rev0.brd, combined_pressure_sensor_rev0.sch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]
